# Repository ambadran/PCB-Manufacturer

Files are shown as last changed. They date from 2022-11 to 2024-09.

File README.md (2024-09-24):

# PCB-Manufacturer

###  Intro
A cnc machine with a kinematic mounting mechanism and specialised code to change head as wanted so as to have access to all the
tools to create a PCB without any human intervention.

### Mechanics
This is a 3 Axis CNC machine made of both metal and 3D printed Parts.
The main driving mechanism is a V-wheel on 2020 profile system with a GT-2 belt driving.
Nema17 Motors was used. The machine was designed for maximal repeatability. 

A 3D printed Kinematic Mounting System was developed to enable the CNC machine to detach and attach to different tool heads on command. The current tool heads are a laser head, a spindle, a Pen marker. The machine automatically attaches to the wanted tool heads without any human intervention.

I also developed an auto-clamping system that clamps the PCB in the bed automatically.

#### Photos
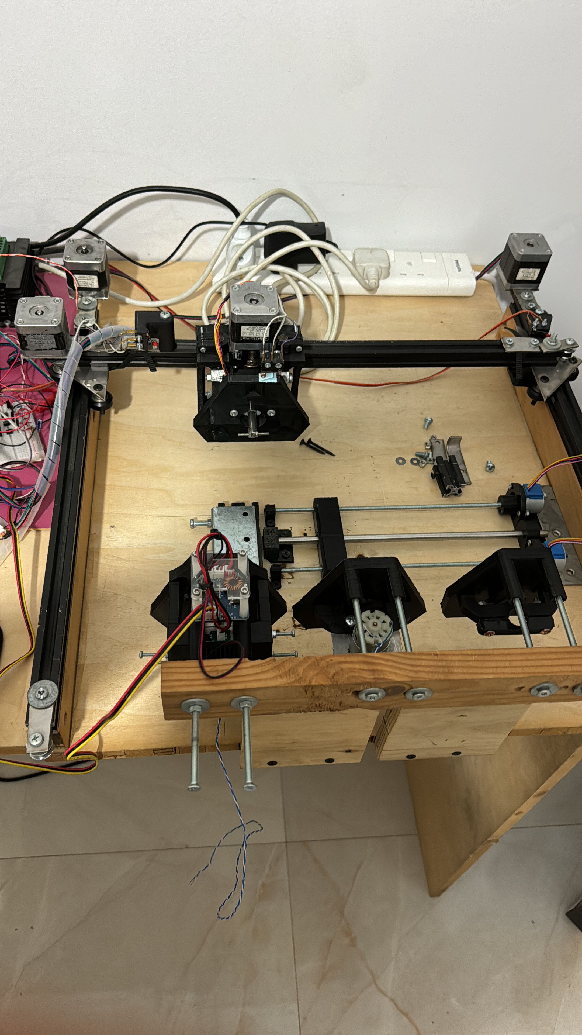
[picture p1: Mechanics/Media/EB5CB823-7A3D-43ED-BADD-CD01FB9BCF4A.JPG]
Overview
[]()

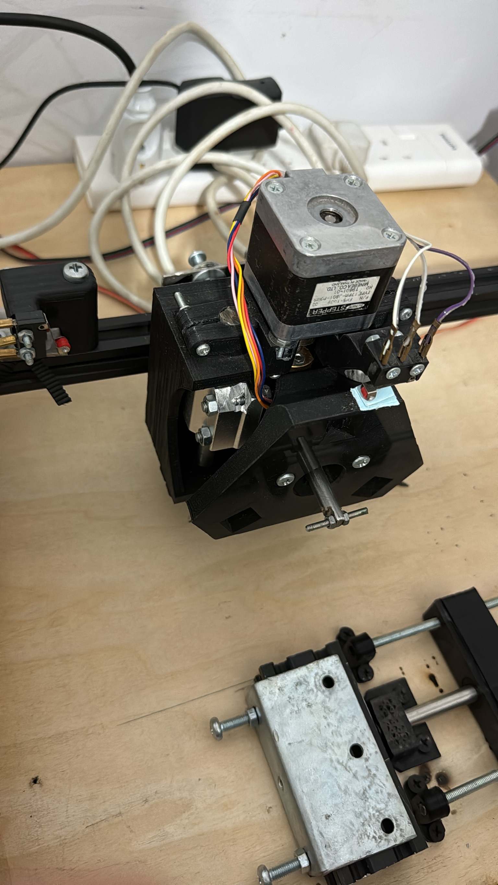
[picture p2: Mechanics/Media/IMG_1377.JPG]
Male Kinematic Mount
[]()

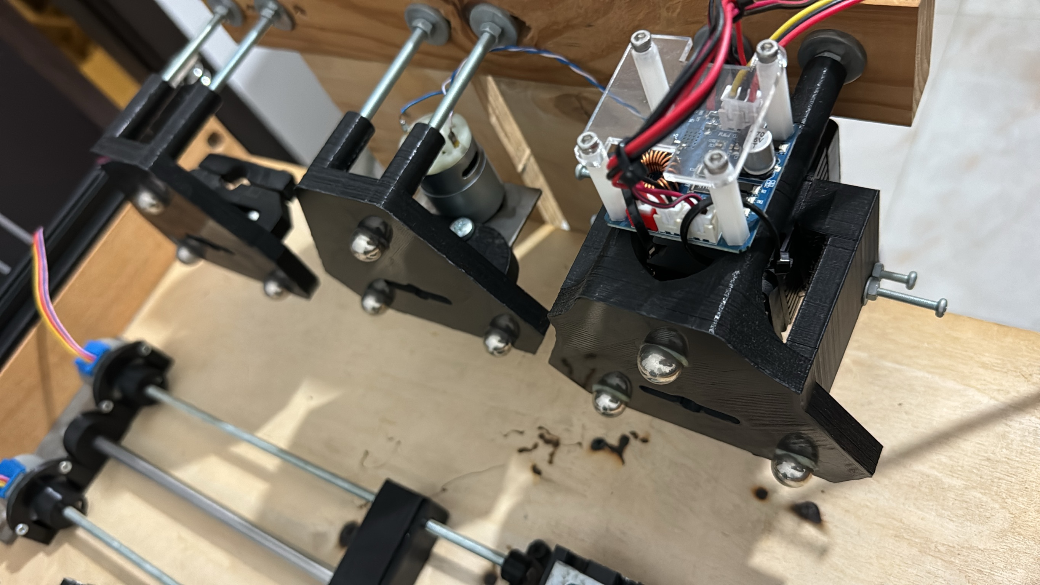
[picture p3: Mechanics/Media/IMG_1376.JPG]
Female Kinematic Mount
[]()

### Electronics
The Main MCU is an Arduino Mega. A Custom GRBL firmware created by me is running on it.

To add a screen monitoring functionality and control the main MCU wirelessly through WiFi, I added a raspberry pi 4 with a 7 inch screen, running mainly UGS Software to monitor the CNC machine.

The Stepper drivers are powerful TB6600 drivers, The end-stops have their own opto-coupler circuit. 
There are 3 power supplies for the CNC machine. one 5v for the main MCU only, one 5v for the raspberry pi. and the third 24v is for the rest of the CNC machine.

This main 24v power supply is switched on using a relay that is controled by the Main MCU. A special G-Code was coded in the firmware to control the main power supply. This adds an important safety layer as the machine is intended to be run remotely.

To relieve the Main MCU from doing everything in the project. I took the liberity to make different circuits for different functions needed for this machine.

I developed a circuit that takes in a 3-bit binary code and the spindle PWM signal from the Main MCU. Then it decodes the 3-bit binary code to allow the PWM to exit through one of the 8 channels that this CNC machine controls. Meaning, the machine can control 8 different end-effectors with PWM, depending on the current 3-bit binary that the MCU outputs.

Another circuit worth mentioning was the stand alone circuit to control the latching mechanism of the kinematic mounting system, where the input to the circuit is just a HIGH/LOW signal from the main MCU triggered by a G-code command `A1` or `A0`. The local MCU does controls the unipolar stepper to latch ON or OFF to the Female kinematic mounts on command and does all the necessary closed-loop logic locally.

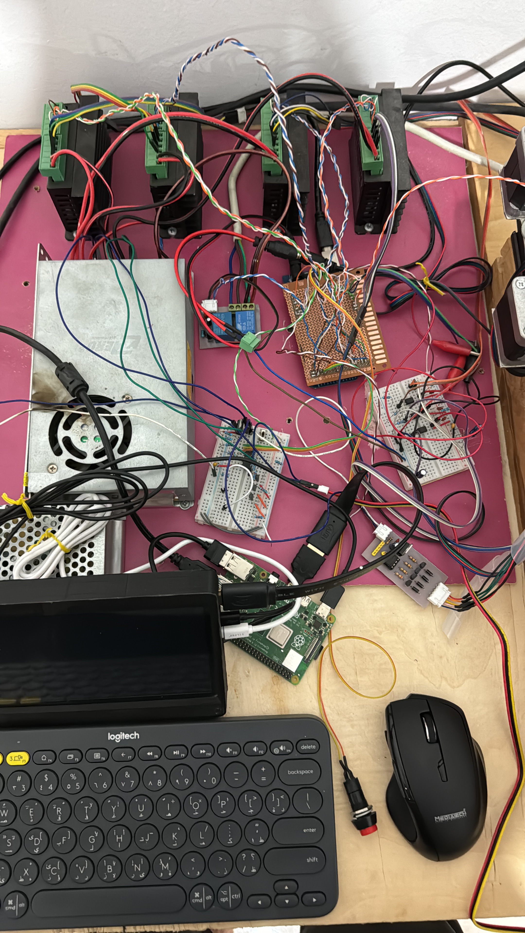
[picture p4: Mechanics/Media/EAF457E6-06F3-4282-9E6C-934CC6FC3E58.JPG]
Electronics
[]()

### Programming
I customized the GRBL firmware from: https://github.com/gnea/grbl 
To accomodate for all the new functionality needed for this CNC machine.
I put in my own G-code commands like `A<x>`, `B<x>` or `C<x>`, that outputs the necessary logic on the Main MCU GPIOs, with no compromise to the original code.

I also developed (from scratch) a complete CAM solution that takes in the gerber files and gives out the G-code ready for my machine. However, due to me deciding to develop from scratch and not use geometry-manipulating libraries like `shapely`. There is alot of corner cases that this version can't handle. 
However, I developed V2 of my all-in-one CAM solution for my CNC machine here: https://github.com/ambadran/PCB-CAM

This version is much much more reliable as to it not being built from scratch.

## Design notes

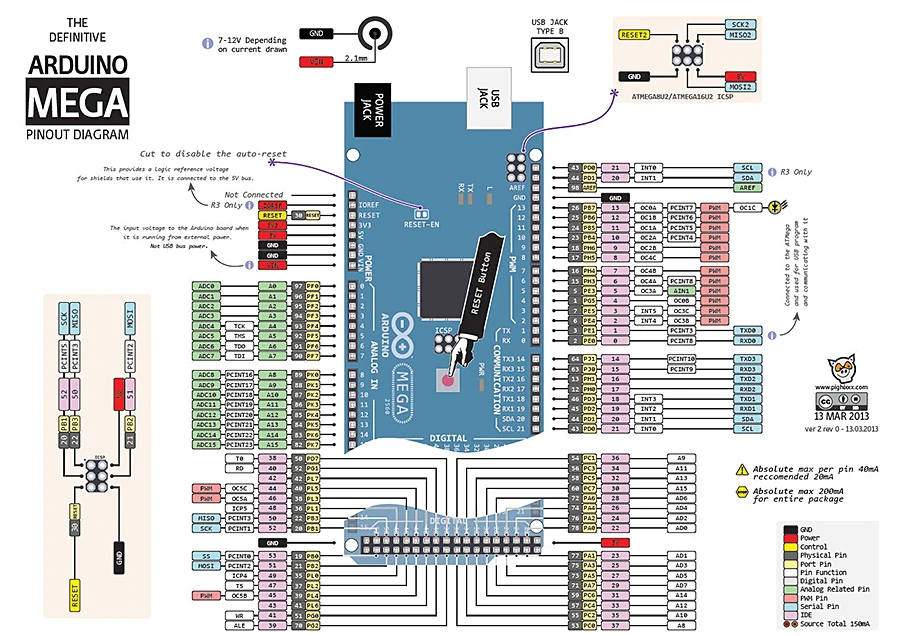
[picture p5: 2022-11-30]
Programming/grbl/photos/arduino-mega-pinout2.png

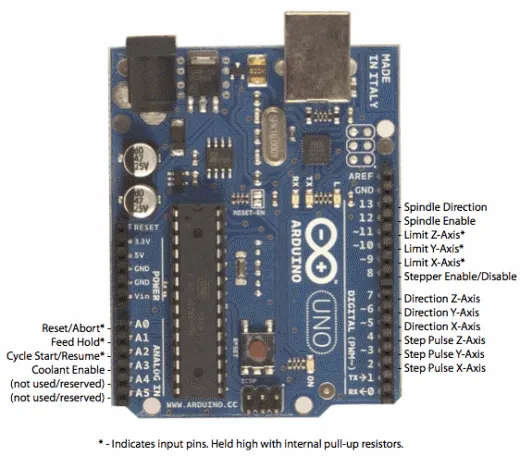
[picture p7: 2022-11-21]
Programming/grbl/photos/grbl_uno_pinout.png

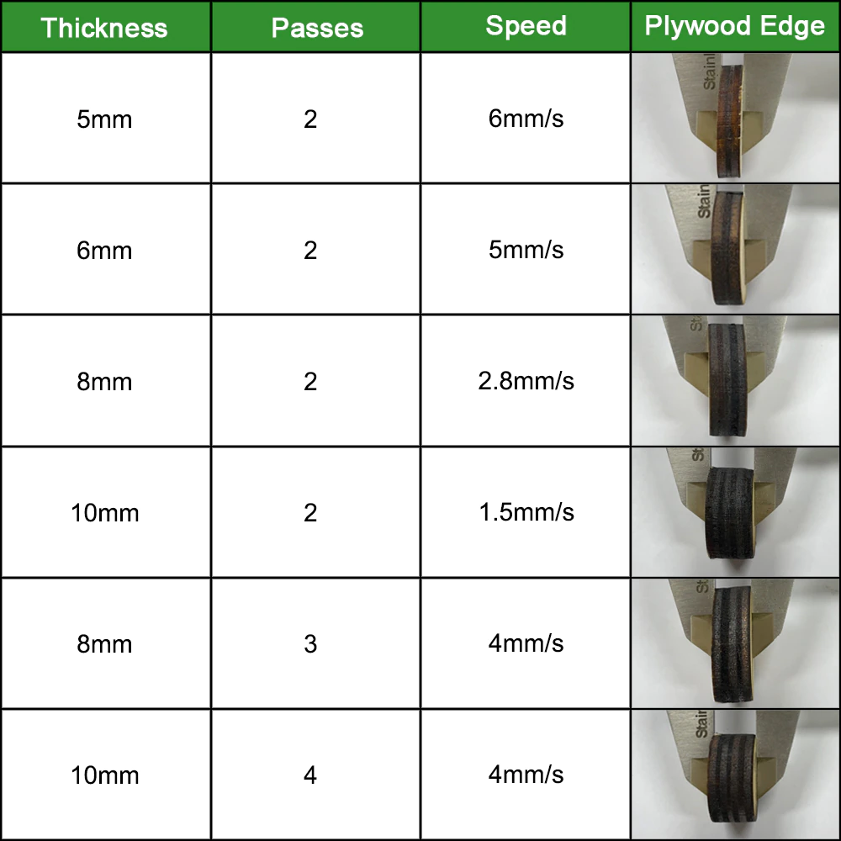
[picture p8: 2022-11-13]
Mechanics/Refrences/Hc2491cd28edc4e7eae7ddbd22f51f325H.jpg.webp

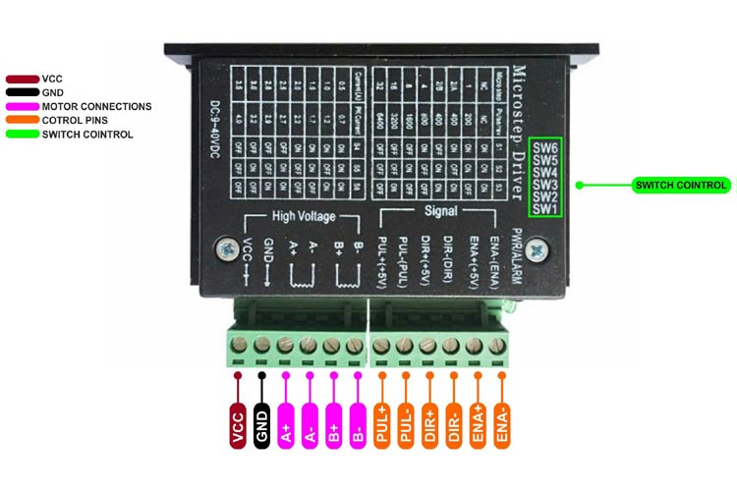
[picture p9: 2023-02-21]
Circuit/bipolar stepper driver/TB6600-Pinout.jpg

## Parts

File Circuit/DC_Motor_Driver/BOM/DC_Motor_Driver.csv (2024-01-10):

Id | Designator | Footprint | Quantity | Designation | Supplier and ref
1 | J1 | JST_EH_S3B-EH_1x03_P2.50mm_Horizontal | 1 | Conn_01x03_Socket
2 | Q3 | TO-92_Inline | 1 | S8550
3 | R3,R2 | R_Axial_DIN0207_L6.3mm_D2.5mm_P7.62mm_Horizontal | 2 | 1k
4 | Q2,Q1,Q4 | TO-92_Inline | 3 | S8050
5 | DC_Motor_Terminal1 | TerminalBlock_bornier-2_P5.08mm | 1 | Screw_Terminal_01x02
6 | Q5 | TO-220-3_Vertical | 1 | IRF540N
7 | R1 | R_Axial_DIN0207_L6.3mm_D2.5mm_P7.62mm_Horizontal | 1 | 10k
8 | CP1 | CP_Radial_D5.0mm_P2.50mm | 1 | 10uF
9 | D1 | D_DO-27_P12.70mm_Horizontal | 1 | SR360
10 | C1 | C_Disc_D5.0mm_W2.5mm_P2.50mm | 1 | 100nF

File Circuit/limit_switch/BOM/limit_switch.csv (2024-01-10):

Id | Designator | Footprint | Quantity | Designation | Supplier and ref
1 | MCU_input1 | JST_EH_S3B-EH_1x03_P2.50mm_Horizontal | 1 | Conn_01x03_Socket
2 | C2,C3,C1 | C_Disc_D5.0mm_W2.5mm_P5.00mm | 3 | 0.1uF
3 | R5,R6,R4 | R_Axial_DIN0207_L6.3mm_D2.5mm_P7.62mm_Horizontal | 3 | 220
4 | Limit_switch_2,Limit_switch_1,Main_PSU_12v1,Limit_switch_3,MCU_5v1 | JST_EH_S2B-EH_1x02_P2.50mm_Horizontal | 5 | Conn_01x02_Socket
5 | OP3,OP2,OP1 | DIP-4_W7.62mm | 3 | PC817
6 | R7,R9,R8 | R_Axial_DIN0207_L6.3mm_D2.5mm_P7.62mm_Horizontal | 3 | 1k
7 | R3,R1,R2 | R_Axial_DIN0207_L6.3mm_D2.5mm_P7.62mm_Horizontal | 3 | 10k

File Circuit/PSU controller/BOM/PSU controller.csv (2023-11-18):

Id | Designator | Footprint | Quantity | Designation | Supplier and ref
1 | D1 | D_DO-34_SOD68_P7.62mm_Horizontal | 1 | D_Schottky
2 | Relay2,Relay1 | Relay_SPDT_SANYOU_SRD_Series_Form_C | 2 | 12v
3 | Q1 | TO-92_Inline | 1 | S8050
4 | CircuitPowerControl1 | PinSocket_1x04_P2.54mm_Vertical | 1 | Conn_01x04_Male
5 | AC_in1,AC_out1 | TerminalBlock_bornier-2_P5.08mm | 2 | Screw_Terminal_01x02
6 | R3 | R_Axial_DIN0207_L6.3mm_D2.5mm_P7.62mm_Horizontal | 1 | 470
7 | R1 | R_Axial_DIN0207_L6.3mm_D2.5mm_P7.62mm_Horizontal | 1 | 10kohm
8 | R2 | R_Axial_DIN0207_L6.3mm_D2.5mm_P7.62mm_Horizontal | 1 | 220
9 | C1 | C_Disc_D5.0mm_W2.5mm_P2.50mm | 1 | 100nF
10 | CP1 | CP_Radial_D5.0mm_P2.00mm | 1 | 100uF
11 | LED1 | D_A-405_P2.54mm_Vertical_AnodeUp | 1 | RED

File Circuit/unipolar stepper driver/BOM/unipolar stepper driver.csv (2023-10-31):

Id | Designator | Footprint | Quantity | Designation | Supplier and ref
1 | Q2,Q4,Q1,Q3 | TO-92_Inline | 4 | S8050
2 | R4,R3 | R_Axial_DIN0207_L6.3mm_D2.5mm_P7.62mm_Horizontal | 2 | 330
3 | C1 | C_Disc_D3.0mm_W2.0mm_P2.50mm | 1 | 10nF
4 | DebuggerPins1,Output1 | PinHeader_1x05_P2.54mm_Vertical | 2 | Conn_01x05_Female
5 | Input1 | PinHeader_1x03_P2.54mm_Vertical | 1 | Conn_01x03_Female
6 | R1,R2 | R_Axial_DIN0207_L6.3mm_D2.5mm_P7.62mm_Horizontal | 2 | 300
7 | D3,D4,D1,D2 | D_DO-34_SOD68_P7.62mm_Horizontal | 4 | DIODE
8 | Debug/UART_pin1 | PinSocket_1x01_P2.54mm_Vertical | 1 | Conn_01x01_Socket
9 | uC1 | DIP-8_W7.62mm | 1 | PIC12F675-IP
10 | PowerRegulator1 | TO-220-3_Vertical | 1 | LM7805_TO220
11 | CP1 | CP_Radial_D5.0mm_P2.50mm | 1 | C_Polarized
12 | R5 | R_Axial_DIN0207_L6.3mm_D2.5mm_P7.62mm_Horizontal | 1 | 10k

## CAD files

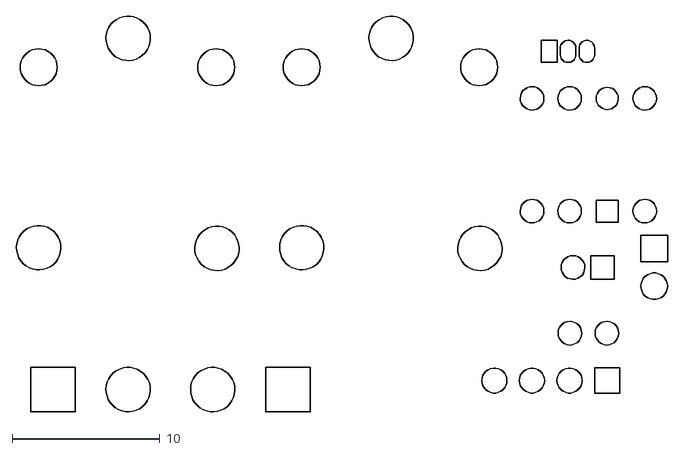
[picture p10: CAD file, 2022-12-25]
Circuit/PSU controller/DXF/PSU controller-B_Cu.dxf
44.0 x 26.7

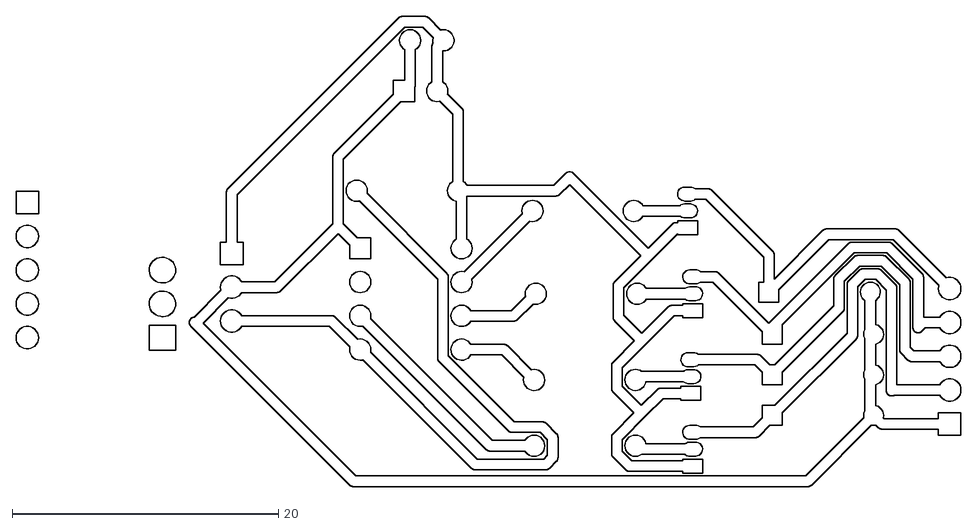
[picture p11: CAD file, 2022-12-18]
Circuit/unipolar stepper driver/DXF/unipolar stepper driver-F_Cu.dxf
71.0 x 35.3

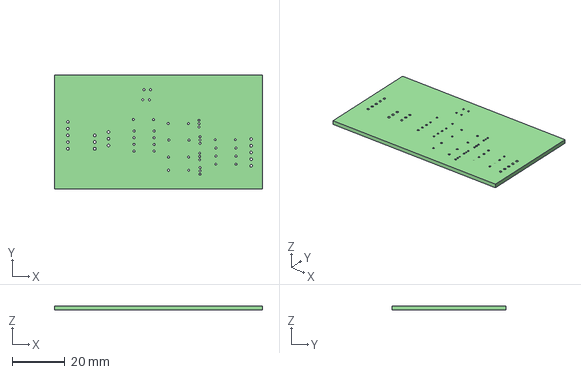
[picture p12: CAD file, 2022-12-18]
Circuit/unipolar stepper driver/STEP/unipolar stepper driver.step
78.7 x 43.2 x 1.60 mm

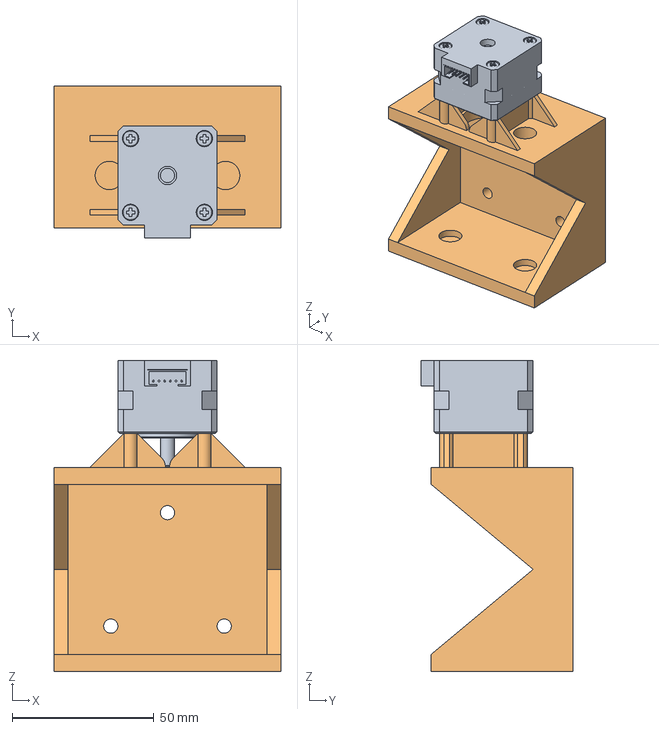
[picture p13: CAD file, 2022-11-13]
Mechanics/3mf/y&z.3mf
80.0 x 53.5 x 109.7 mm
MINEBEA_05701202

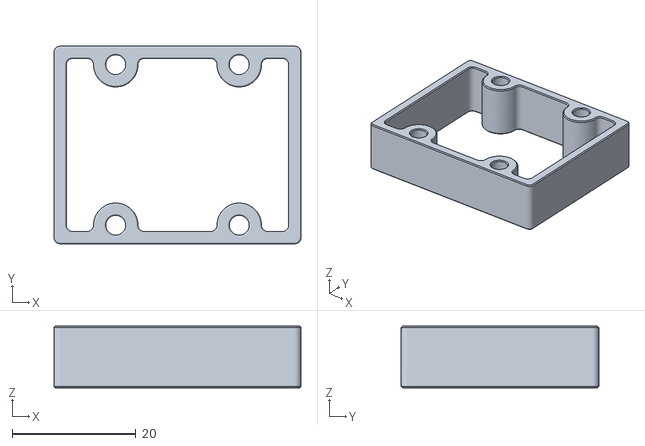
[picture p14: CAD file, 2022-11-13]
Mechanics/reference CAD/Tool Changer/ToolChanger-master/Hemera Direct Tool/STLs/V6_Receiver_Top.stl
40.0 x 32.0 x 10.0

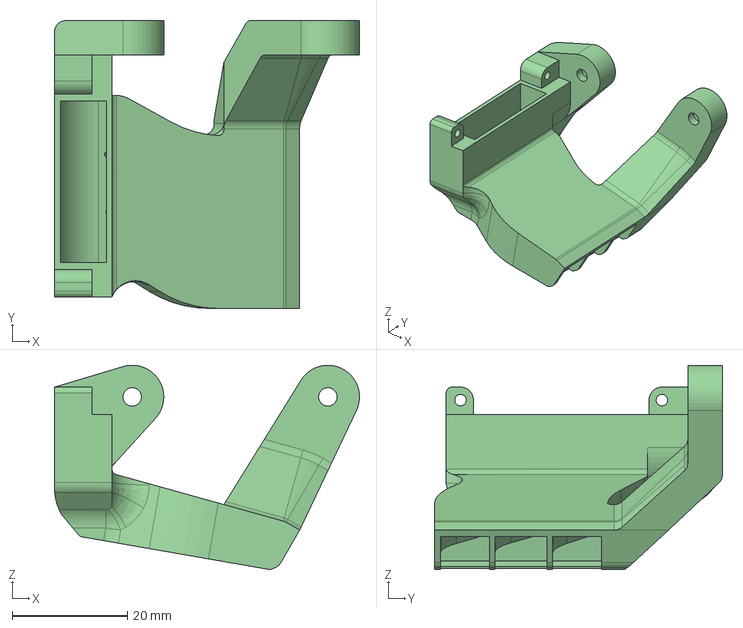
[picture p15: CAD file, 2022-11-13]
Mechanics/reference CAD/Tool Changer/ToolChanger-master/Hemera Direct Tool/STPs/Hemera_PCF_Duct_-_Volcano.step
53.0 x 50.0 x 35.5 mm

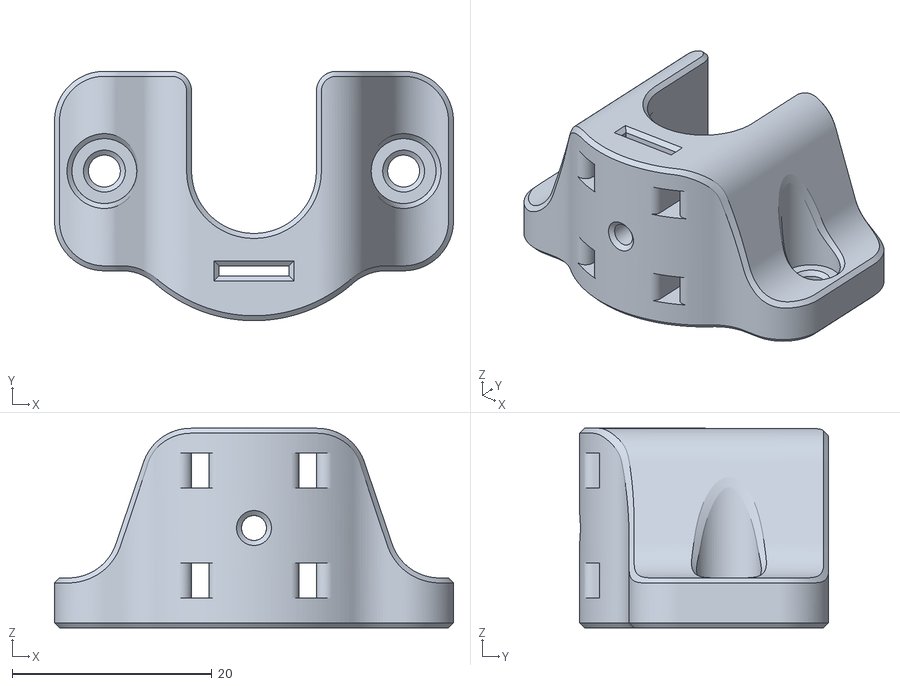
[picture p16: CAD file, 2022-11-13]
Mechanics/reference CAD/Tool Changer/ToolChanger-master/STLs/X-Carriage Cables.stl
40.0 x 25.0 x 20.0

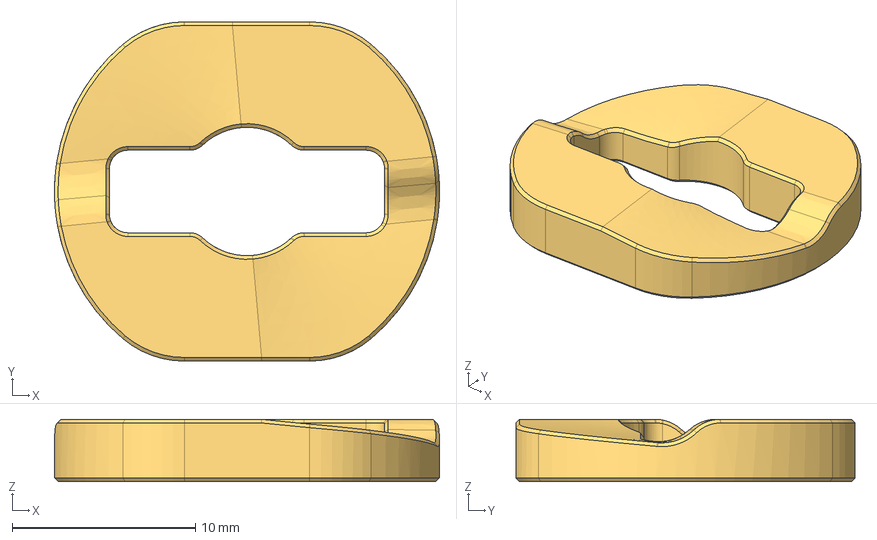
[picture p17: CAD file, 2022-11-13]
Mechanics/reference CAD/Tool Changer/ToolChanger-master/STPs/TC-RAMP-6MM 1.3.step
21.0 x 18.5 x 3.40 mm

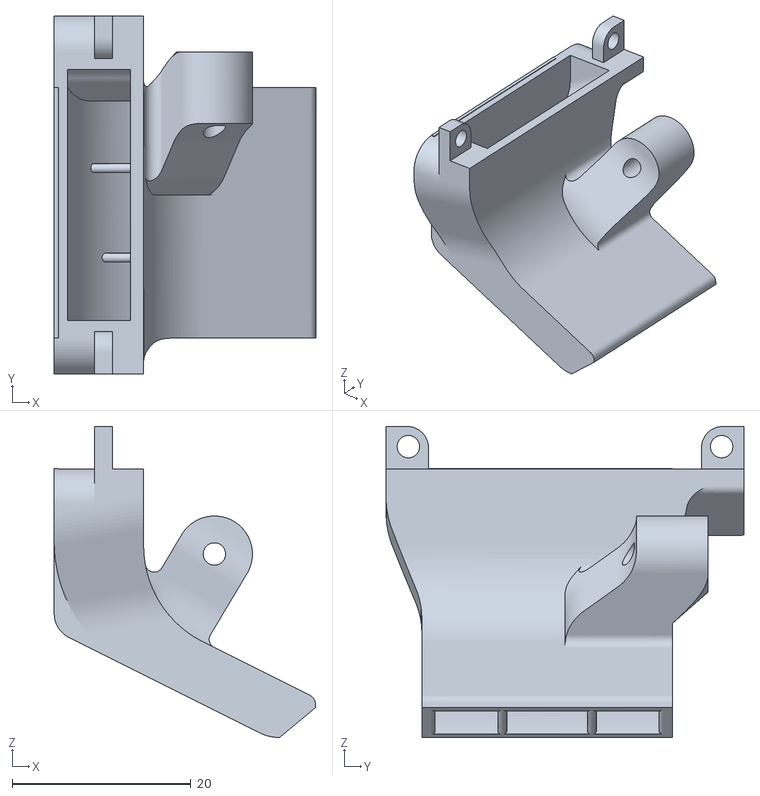
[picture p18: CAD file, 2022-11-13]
Mechanics/reference CAD/Tool Changer/ToolChanger-master/V6 Tool/STLs/V6 PCF Duct (Winsinn).stl
29.2 x 40.0 x 34.8

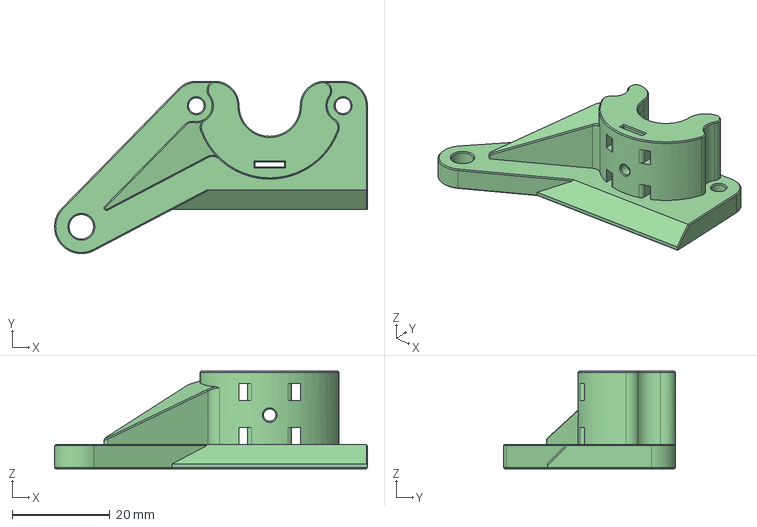
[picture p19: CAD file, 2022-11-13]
Mechanics/reference CAD/Tool Changer/ToolChanger-master/V6 Tool/STPs/V6 Dock Cables.step
64.0 x 35.2 x 20.0 mm

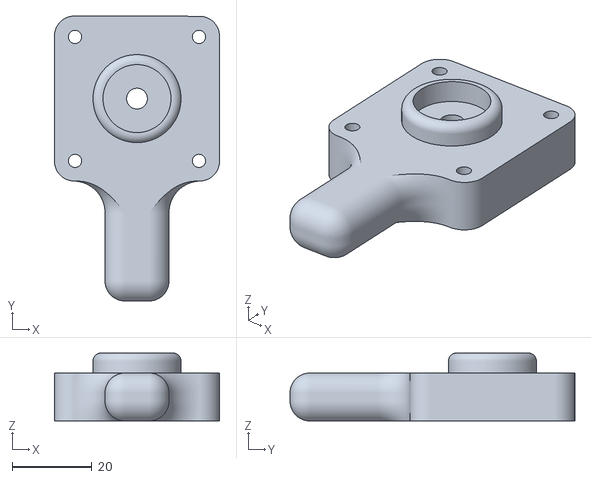
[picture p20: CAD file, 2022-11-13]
Mechanics/STLs/Nema 17 holes Spacer.stl
41.3 x 71.3 x 17.0

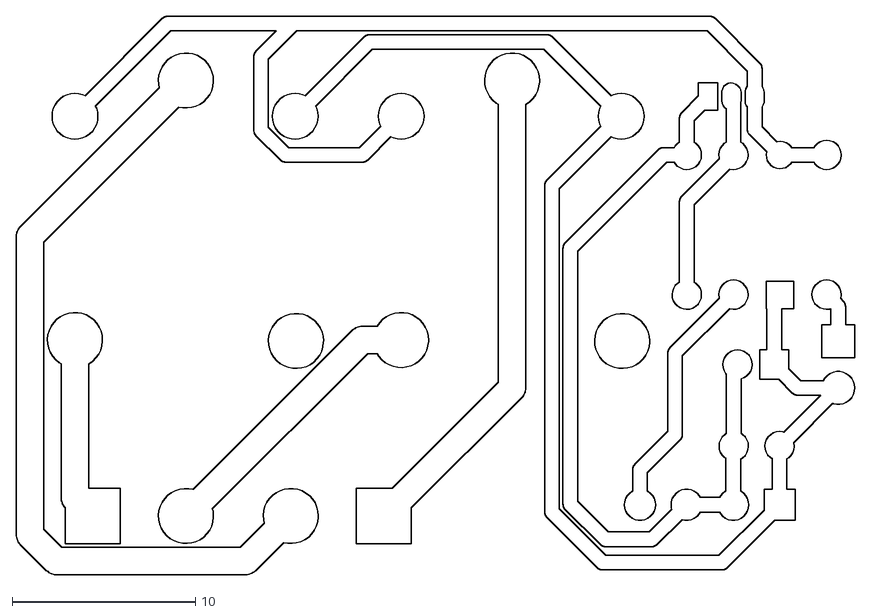
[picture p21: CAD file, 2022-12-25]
Circuit/PSU controller/DXF/PSU controller-F_Cu.dxf
45.7 x 30.4

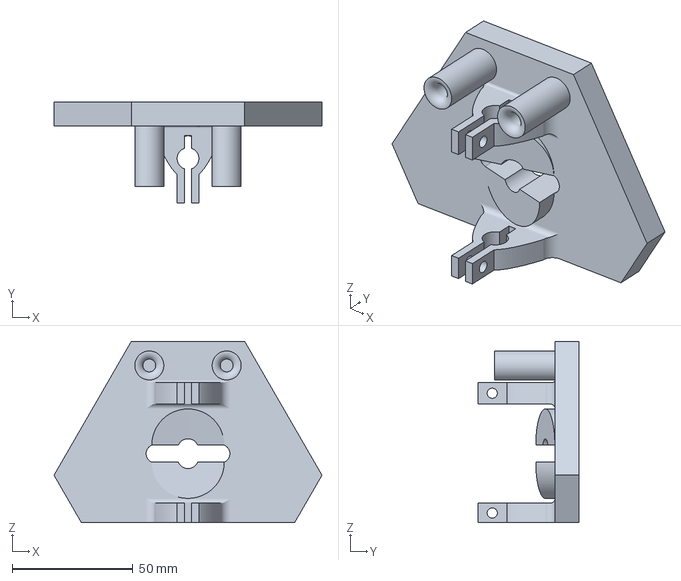
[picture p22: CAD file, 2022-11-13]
Mechanics/3mf/female.3mf
110.9 x 42.0 x 75.1 mm

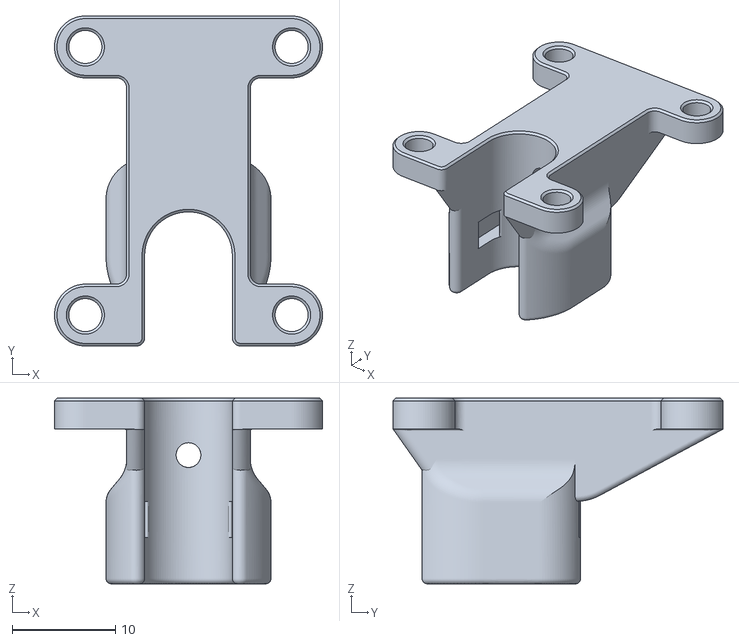
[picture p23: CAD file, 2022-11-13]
Mechanics/reference CAD/Tool Changer/ToolChanger-master/Hemera Direct Tool/STLs/V6_Cable_Support.stl
26.0 x 32.0 x 18.0

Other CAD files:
Mechanics/reference CAD/Tool Changer/ToolChanger-master/Hemera Direct Tool/STPs/TC-V6-HEMERA-DOCK-BRACE.step
Mechanics/reference CAD/Tool Changer/ToolChanger-master/STLs/Tool-Changer Cover Triangle.stl
Mechanics/reference CAD/Tool Changer/ToolChanger-master/STPs/TC-MOD0.5-40T-GEAR 1.1.step
Mechanics/reference CAD/Tool Changer/ToolChanger-master/V6 Tool/STLs/V6 Dock Cables(Mirror).stl
Circuit/PSU controller/DXF/PSU controller-B_Paste.dxf
Circuit/PSU controller/DXF/PSU controller-B_Silkscreen.dxf
Circuit/PSU controller/DXF/PSU controller-Edge_Cuts.dxf
Circuit/PSU controller/DXF/PSU controller-F_Paste.dxf
Circuit/PSU controller/DXF/PSU controller-F_Silkscreen.dxf
Mechanics/3mf/Male.3mf
Mechanics/3mf/Y and Z.3mf
Mechanics/3mf/Y-Bracket.3mf
Mechanics/STLs/laser_module_k_mount.stl
Mechanics/reference CAD/Tool Changer/ToolChanger-master/Hemera Direct Tool/STLs/Hemera_PCF_Bracket.stl
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

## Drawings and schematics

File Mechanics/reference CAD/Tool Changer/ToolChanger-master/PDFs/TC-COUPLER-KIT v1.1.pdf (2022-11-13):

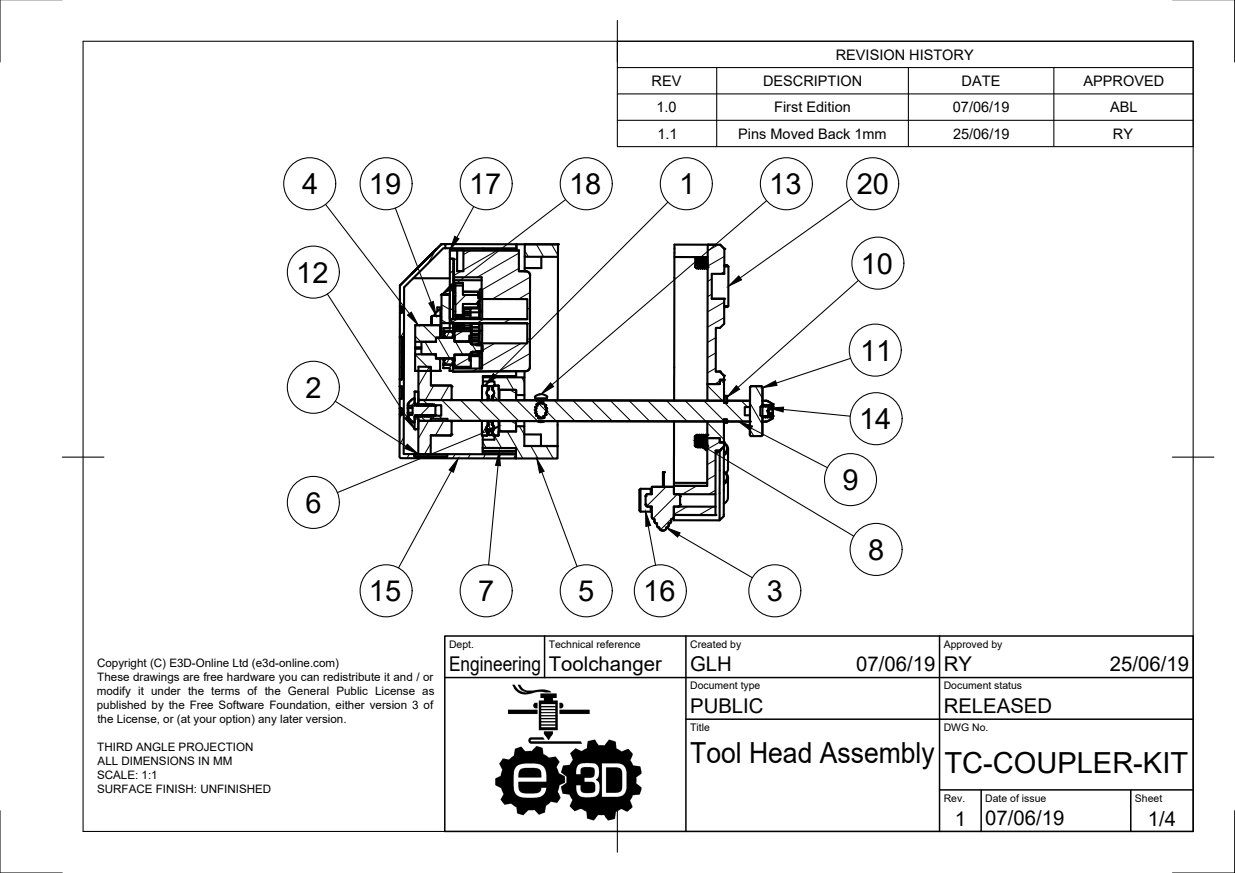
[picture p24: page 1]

REVISION HISTORY

REV | DESCRIPTION | DATE | APPROVED
1.0 | First Edition | 07/06/19 | ABL
1.1 | Pins Moved Back 1mm | 25/06/19 | RY

Dept. Engineering | Technical reference Toolchanger | Created by GLH 07/06/19 | Approved by RY 25/06/19

Copyright (C) E3D-Online Ltd (e3d-online.com)
These drawings are free hardware you can redistribute it and / or modify it under the terms of the General Public License as published by the Free Software Foundation, either version 3 of

Document type PUBLIC | Document status RELEASED

the License, or (at your option) any later version.

Title | DWG No. TC-COUPLER-KIT Tool Head Assembly

THIRD ANGLE PROJECTION
ALL DIMENSIONS IN MM
SCALE: 1:1
SURFACE FINISH: UNFINISHED

Rev. 1 | Date of issue 07/06/19 | Sheet

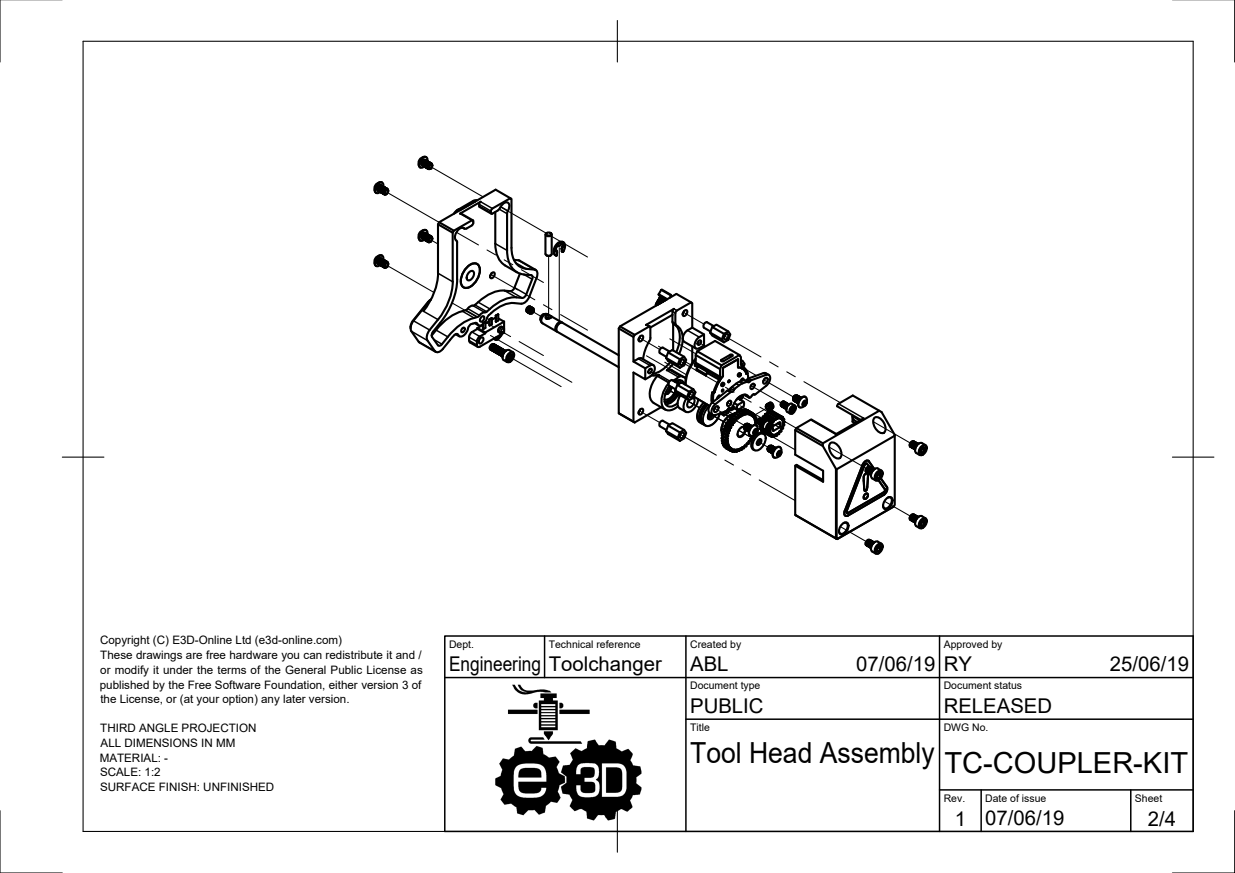
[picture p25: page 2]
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

Dept. Engineering | Technical reference Toolchanger | Created by ABL 07/06/19 | Approved by RY 25/06/19

Document type PUBLIC | Document status RELEASED

the License, or (at your option) any later version.

THIRD ANGLE PROJECTION
ALL DIMENSIONS IN MM
MATERIAL: -
SCALE: 1:2
SURFACE FINISH: UNFINISHED

Title | DWG No. TC-COUPLER-KIT Tool Head Assembly

Rev. | Date of issue | Sheet

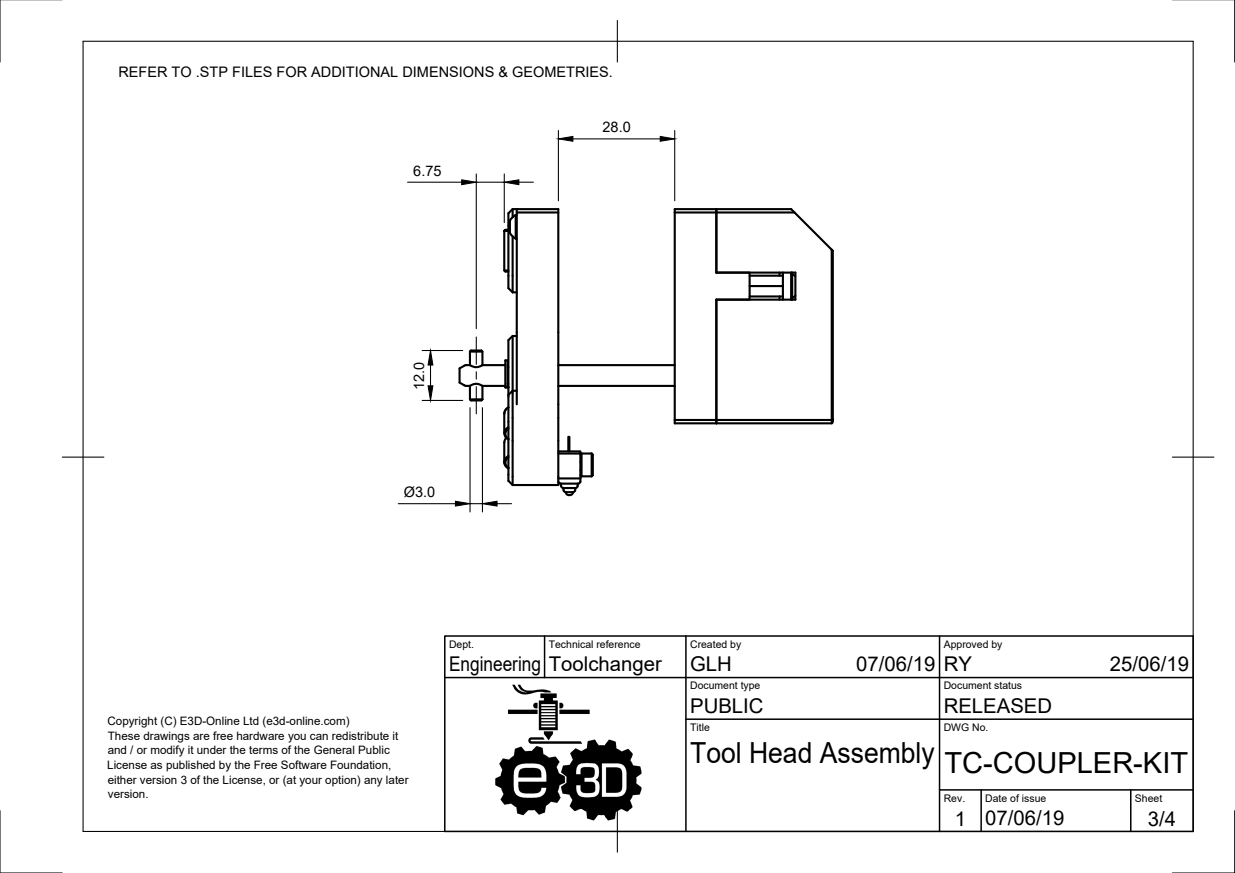
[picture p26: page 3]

REFER TO .STP FILES FOR ADDITIONAL DIMENSIONS & GEOMETRIES.

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

Document type PUBLIC | Document status RELEASED

Copyright (C) E3D-Online Ltd (e3d-online.com)
These drawings are free hardware you can redistribute it
and / or modify it under the terms of the General Public
License as published by the Free Software Foundation,
either version 3 of the License, or (at your option) any later
version.

Title | DWG No. TC-COUPLER-KIT Tool Head Assembly

Rev. | Date of issue | Sheet

Dept. Engineering | Technical reference Toolchanger | Created by GLH 07/06/19 | Approved by RY 25/06/19
| | Document type PUBLIC | Document status RELEASED
| | Title | DWG No. TC-COUPLER-KIT Tool Head Assembly
Rev. | Date of issue | Sheet

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

### Parts List

Item | Qty | Description
1 | 1 | F5-12M Thrust Bearing
2 | 1 | 40T Gear M0D 0.5
3 | 1 | Endstop Switch
4 | 1 | 20T Gear MOD 0.5
5 | 1 | TC-BACK
6 | 1 | MR105RS Bearing
7 | 1 | 8mm Standoff
8 | 7 | M4 5mm Button Head Screw
9 | 1 | Tool Coupler Shaft
10 | 1 | E-Clip
11 | 1 | 12mm x 3mm Dowel Pin
12 | 1 | M3 Washer
13 | 5 | M3 4mm Socket Head Screw
14 | 2 | M3 3mm Grub Screw
15 | 1 | Printed Cover
16 | 1 | M3 10mm Socket Head Screw
17 | 1 | Stepper Motor
18 | 1 | Motor Bracket
19 | 2 | M2.5 5mm Socket Head Screw
20 | 1 | TC-FACE-AS

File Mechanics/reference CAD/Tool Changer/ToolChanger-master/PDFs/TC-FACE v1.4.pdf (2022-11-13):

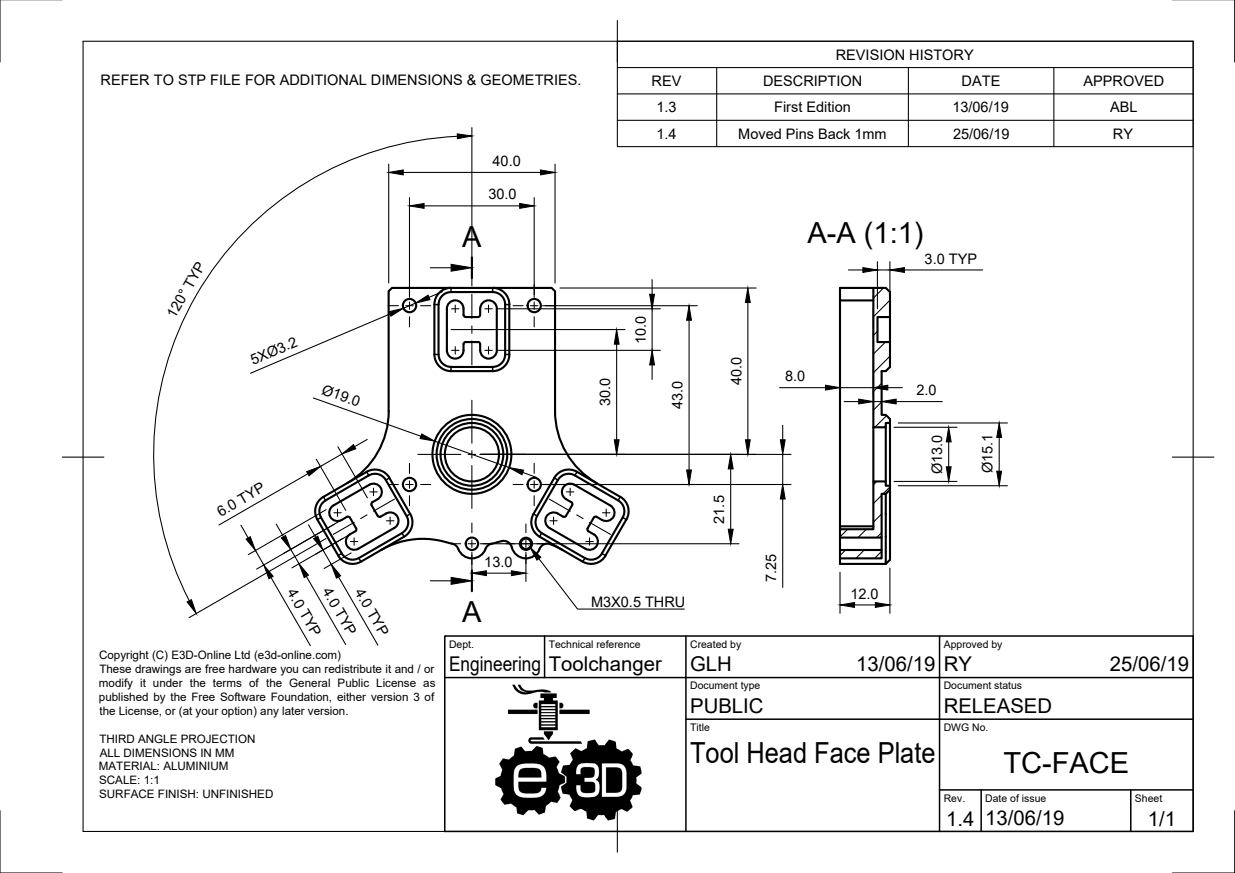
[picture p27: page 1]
M3X0.5 THRU; 120° TYP 43.0 Ø13.0 Ø15.1; 3.0 TYP; 6.0 TYP

REVISION HISTORY

REFER TO STP FILE FOR ADDITIONAL DIMENSIONS & GEOMETRIES.

REV | DESCRIPTION | DATE | APPROVED
1.3 | First Edition | 13/06/19 | ABL
1.4 | Moved Pins Back 1mm | 25/06/19 | RY

4.0 TYP 4.0 TYP 4.0 TYP

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

Dept. Engineering | Technical reference Toolchanger | Created by GLH 13/06/19 | Approved by RY 25/06/19

Document type PUBLIC | Document status RELEASED

the License, or (at your option) any later version.

Title | DWG No. TC-FACE Tool Head Face Plate

THIRD ANGLE PROJECTION
ALL DIMENSIONS IN MM
MATERIAL: ALUMINIUM
SCALE: 1:1
SURFACE FINISH: UNFINISHED

Rev. 1.4 | Date of issue 13/06/19 | Sheet 1/1

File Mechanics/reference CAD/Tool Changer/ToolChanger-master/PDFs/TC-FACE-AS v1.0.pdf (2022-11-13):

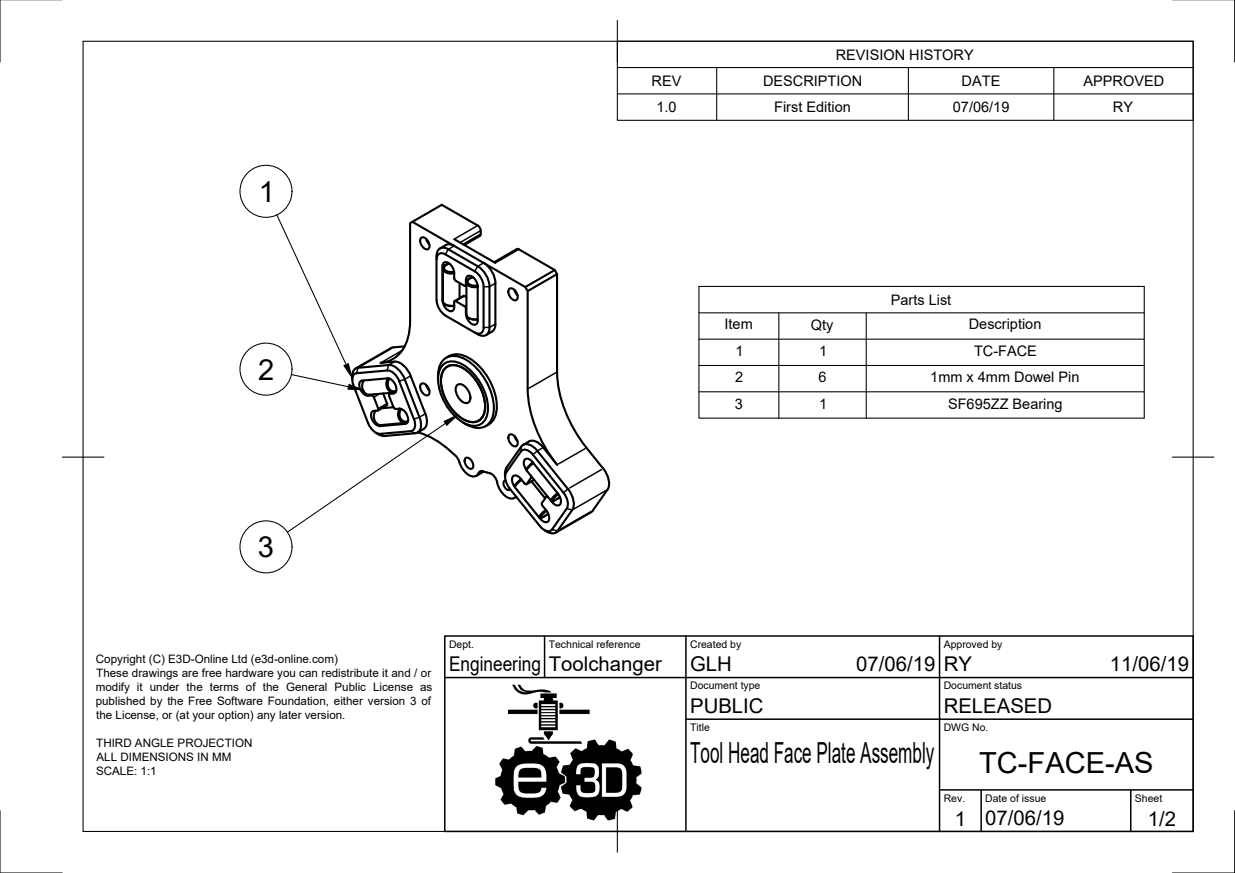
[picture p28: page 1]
Parts List

REVISION HISTORY

REV | DESCRIPTION | DATE | APPROVED
1.0 | First Edition | 07/06/19 | RY

Item | Qty | Description
1 | 1 | TC-FACE
2 | 6 | 1mm x 4mm Dowel Pin
3 | 1 | SF695ZZ Bearing

Dept. Engineering | Technical reference Toolchanger | Created by GLH 07/06/19 | Approved by RY 11/06/19

Copyright (C) E3D-Online Ltd (e3d-online.com)
These drawings are free hardware you can redistribute it and / or modify it under the terms of the General Public License as published by the Free Software Foundation, either version 3 of

Document type PUBLIC | Document status RELEASED

the License, or (at your option) any later version.

Title | DWG No. TC-FACE-AS Tool Head Face Plate Assembly

THIRD ANGLE PROJECTION
ALL DIMENSIONS IN MM
SCALE: 1:1

Rev. 1 | Date of issue 07/06/19 | Sheet 1/2

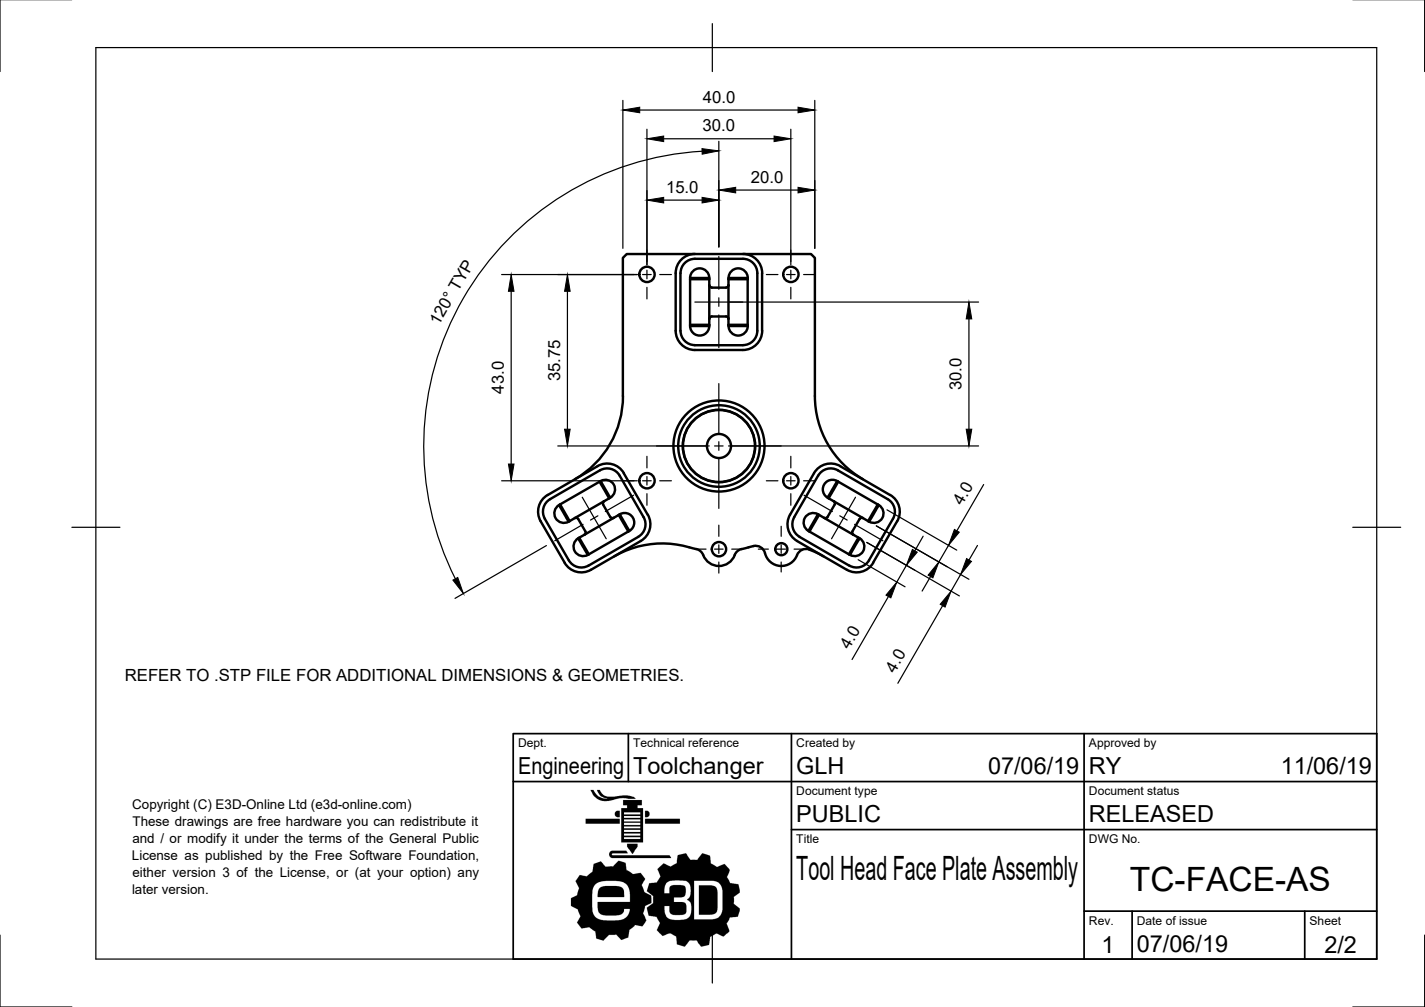
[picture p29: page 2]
120° TYP

REFER TO .STP FILE FOR ADDITIONAL DIMENSIONS & GEOMETRIES.

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

Document type PUBLIC | Document status RELEASED

Copyright (C) E3D-Online Ltd (e3d-online.com)
These drawings are free hardware you can redistribute it
and / or modify it under the terms of the General Public
License as published by the Free Software Foundation,
either version 3 of the License, or (at your option) any
later version.

Title | DWG No. TC-FACE-AS Tool Head Face Plate Assembly

Rev. 1 | Date of issue 07/06/19 | Sheet 2/2

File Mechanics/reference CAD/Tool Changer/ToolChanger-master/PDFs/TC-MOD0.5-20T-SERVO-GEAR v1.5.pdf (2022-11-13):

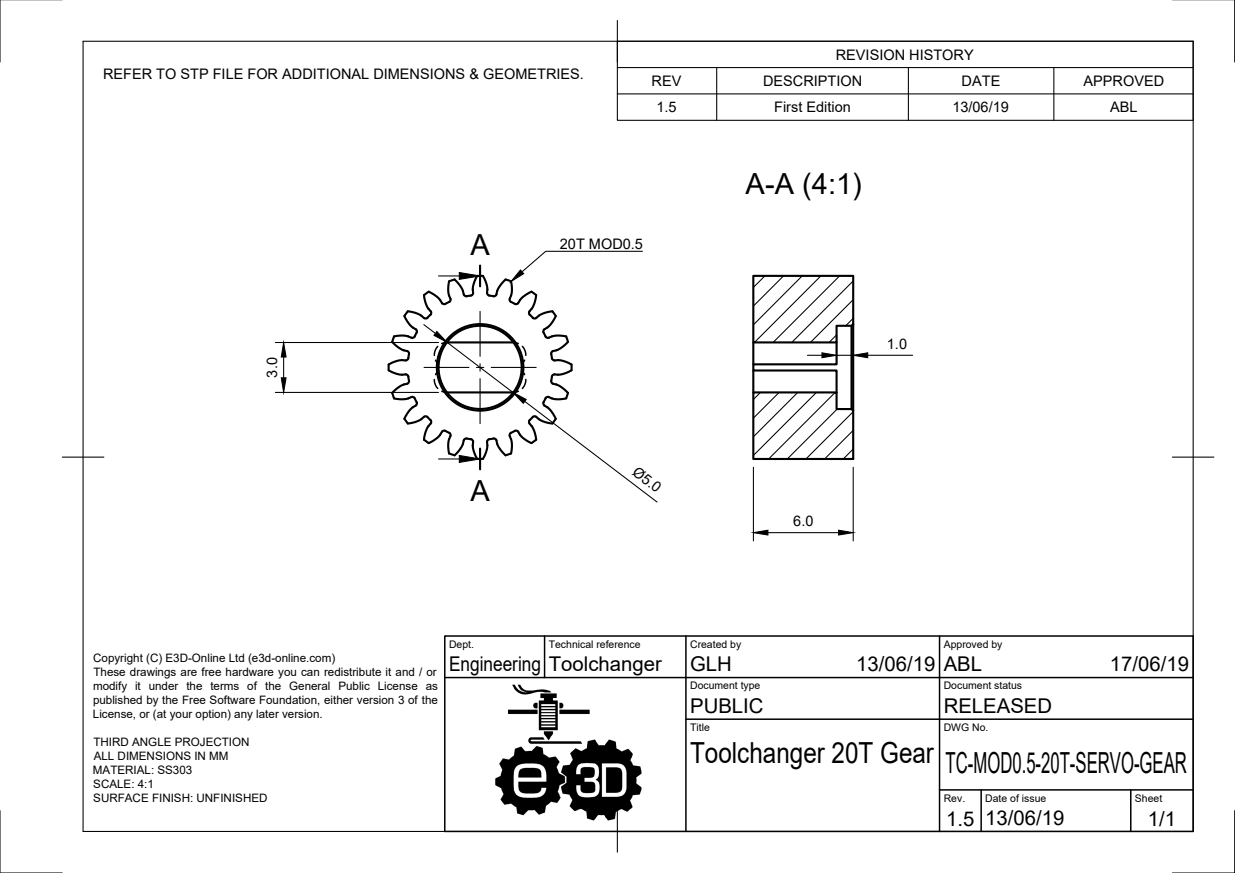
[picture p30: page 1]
20T MOD0.5

REVISION HISTORY

REFER TO STP FILE FOR ADDITIONAL DIMENSIONS & GEOMETRIES.

REV | DESCRIPTION | DATE | APPROVED
1.5 | First Edition | 13/06/19 | ABL

Dept. Engineering | Technical reference Toolchanger | Created by GLH 13/06/19 | Approved by ABL 17/06/19

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

Document type PUBLIC | Document status RELEASED

License, or (at your option) any later version.

Title | DWG No. TC-MOD0.5-20T-SERVO-GEAR Toolchanger 20T Gear

THIRD ANGLE PROJECTION
ALL DIMENSIONS IN MM
MATERIAL: SS303
SCALE: 4:1
SURFACE FINISH: UNFINISHED

Rev. 1.5 | Date of issue 13/06/19 | Sheet 1/1

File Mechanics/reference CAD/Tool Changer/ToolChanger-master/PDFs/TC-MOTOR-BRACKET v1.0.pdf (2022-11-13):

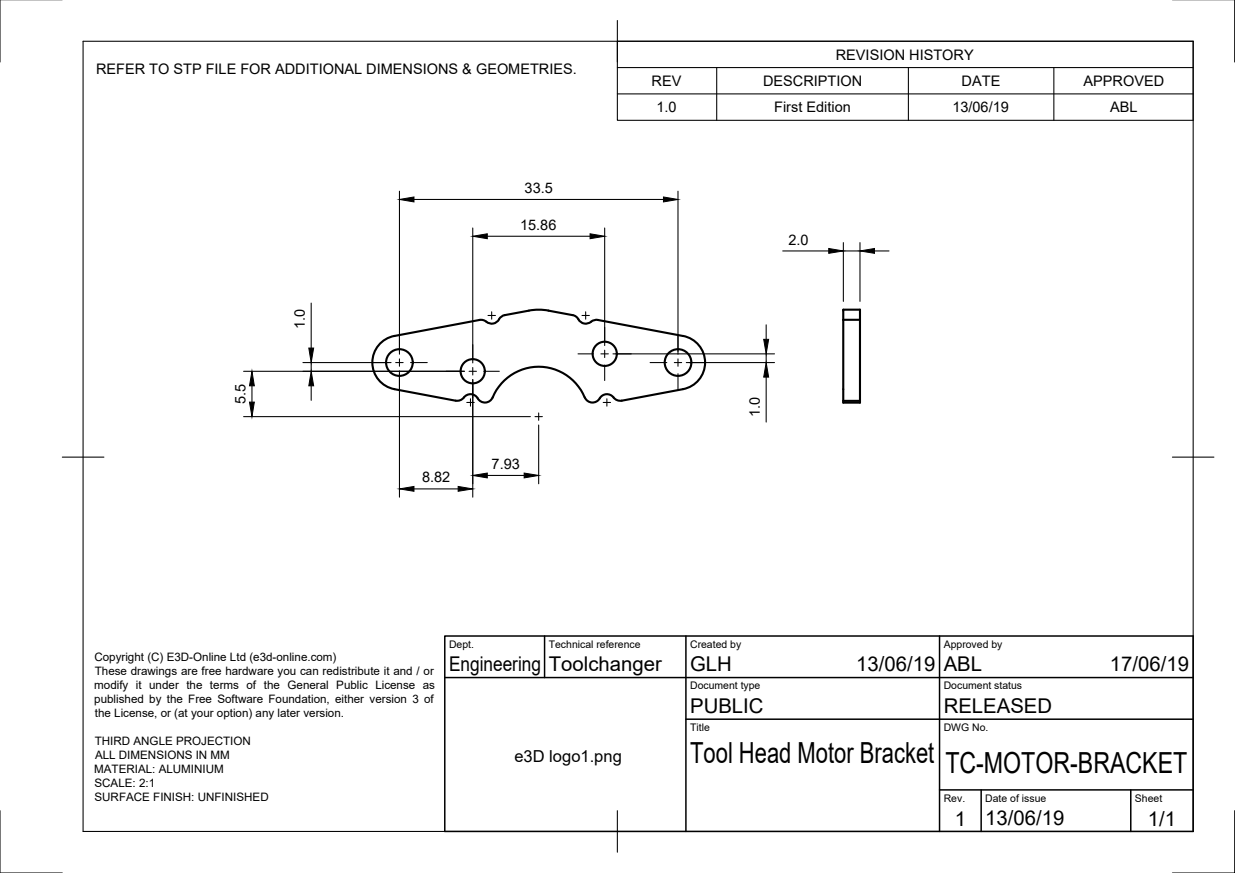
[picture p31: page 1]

REVISION HISTORY

REFER TO STP FILE FOR ADDITIONAL DIMENSIONS & GEOMETRIES.

REV | DESCRIPTION | DATE | APPROVED
1.0 | First Edition | 13/06/19 | ABL

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

e3D logo1.png | | Document type PUBLIC | Document status RELEASED

the License, or (at your option) any later version.

Title | DWG No. TC-MOTOR-BRACKET Tool Head Motor Bracket

THIRD ANGLE PROJECTION
ALL DIMENSIONS IN MM
MATERIAL: ALUMINIUM
SCALE: 2:1
SURFACE FINISH: UNFINISHED

Rev. 1 | Date of issue 13/06/19 | Sheet 1/1

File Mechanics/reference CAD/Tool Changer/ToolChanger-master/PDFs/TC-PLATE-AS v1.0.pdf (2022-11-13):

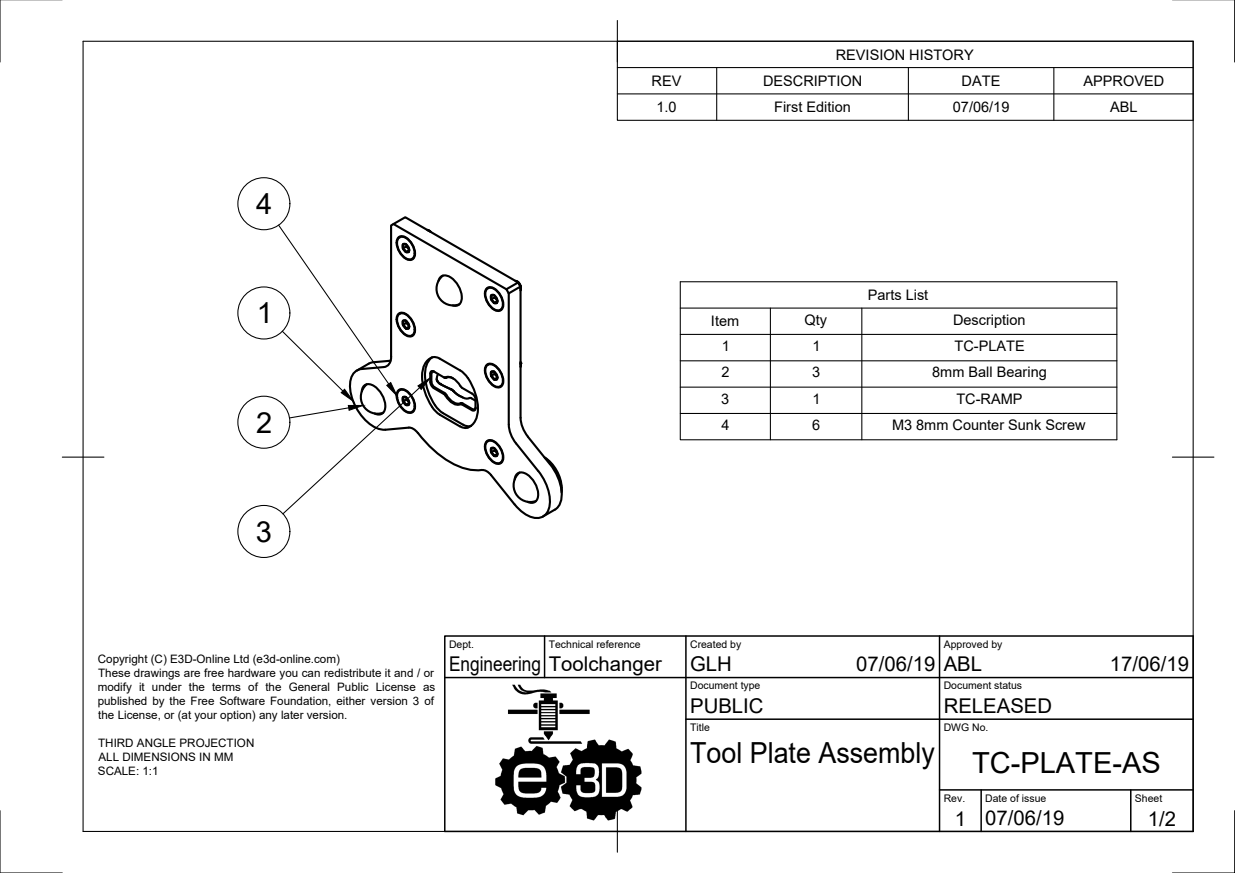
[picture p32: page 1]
Parts List

REVISION HISTORY

REV | DESCRIPTION | DATE | APPROVED
1.0 | First Edition | 07/06/19 | ABL

Item | Qty | Description
1 | 1 | TC-PLATE
2 | 3 | 8mm Ball Bearing
3 | 1 | TC-RAMP
4 | 6 | M3 8mm Counter Sunk Screw

Dept. Engineering | Technical reference Toolchanger | Created by GLH 07/06/19 | Approved by ABL 17/06/19

Copyright (C) E3D-Online Ltd (e3d-online.com)
These drawings are free hardware you can redistribute it and / or modify it under the terms of the General Public License as published by the Free Software Foundation, either version 3 of

Document type PUBLIC | Document status RELEASED

the License, or (at your option) any later version.

Title | DWG No. TC-PLATE-AS Tool Plate Assembly

THIRD ANGLE PROJECTION
ALL DIMENSIONS IN MM
SCALE: 1:1

Rev. 1 | Date of issue 07/06/19 | Sheet 1/2

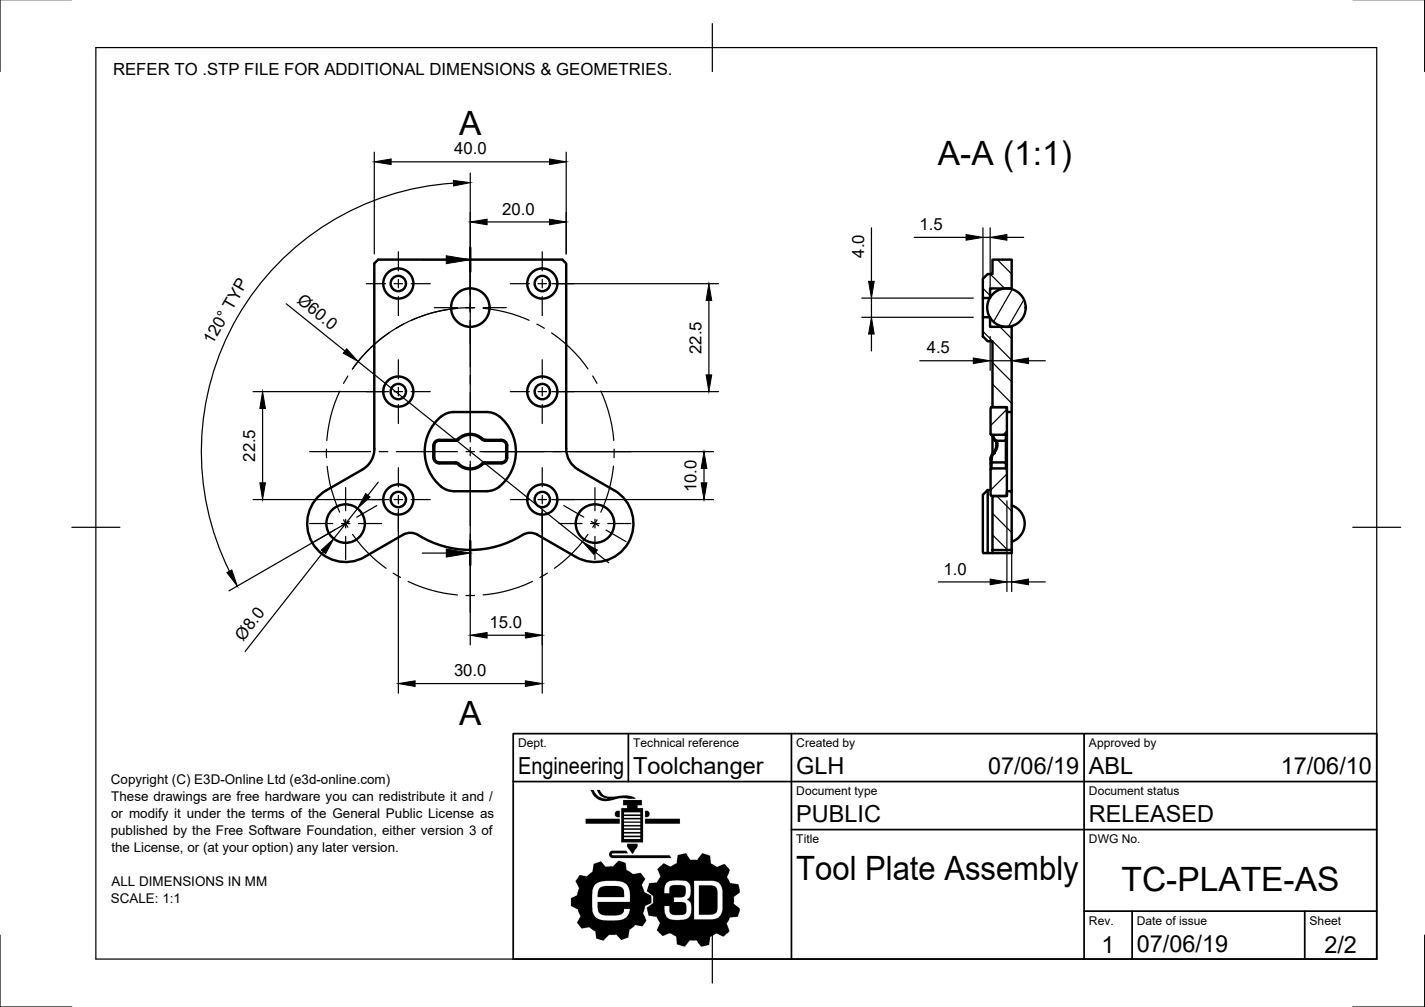
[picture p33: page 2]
Ø60.0 120° TYP

REFER TO .STP FILE FOR ADDITIONAL DIMENSIONS & GEOMETRIES.

Dept. Engineering | Technical reference Toolchanger | Created by GLH 07/06/19 | Approved by ABL Copyright (C) E3D-Online Ltd (e3d-online.com) 17/06/10

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

Document type PUBLIC | Document status RELEASED

the License, or (at your option) any later version.

Title | DWG No. TC-PLATE-AS Tool Plate Assembly

ALL DIMENSIONS IN MM
SCALE: 1:1

Rev. 1 | Date of issue 07/06/19 | Sheet 2/2

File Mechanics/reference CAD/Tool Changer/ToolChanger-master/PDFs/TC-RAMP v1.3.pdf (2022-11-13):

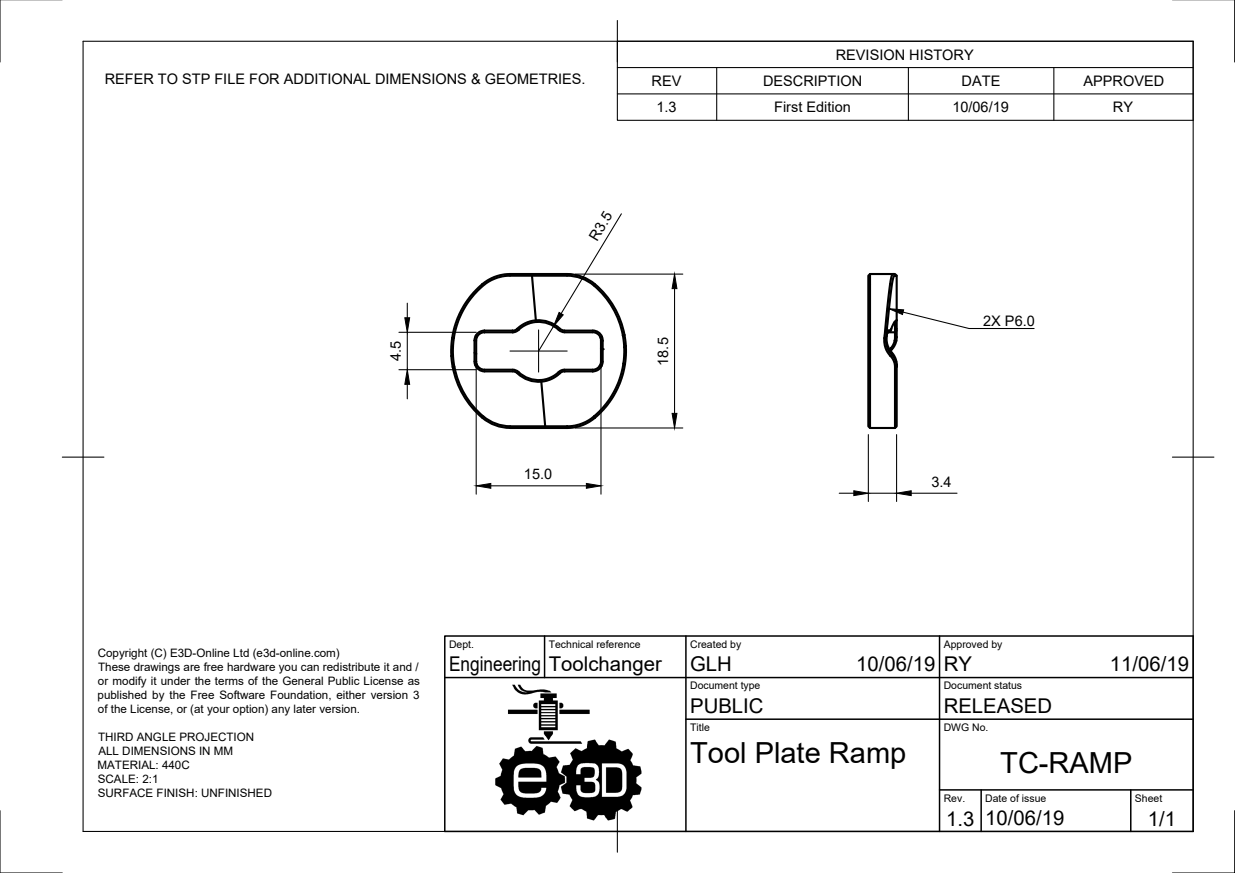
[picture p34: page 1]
REFER TO STP FILE FOR ADDITIONAL DIMENSIONS & GEOMETRIES.

REVISION HISTORY

REV | DESCRIPTION | DATE | APPROVED
1.3 | First Edition | 10/06/19 | RY

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

Dept. Engineering | Technical reference Toolchanger | Created by GLH 10/06/19 | Approved by RY 11/06/19

Document type PUBLIC | Document status RELEASED

of the License, or (at your option) any later version.

THIRD ANGLE PROJECTION
ALL DIMENSIONS IN MM
MATERIAL: 440C
SCALE: 2:1
SURFACE FINISH: UNFINISHED

Title | DWG No. TC-RAMP Tool Plate Ramp

Rev. 1.3 | Date of issue 10/06/19 | Sheet 1/1

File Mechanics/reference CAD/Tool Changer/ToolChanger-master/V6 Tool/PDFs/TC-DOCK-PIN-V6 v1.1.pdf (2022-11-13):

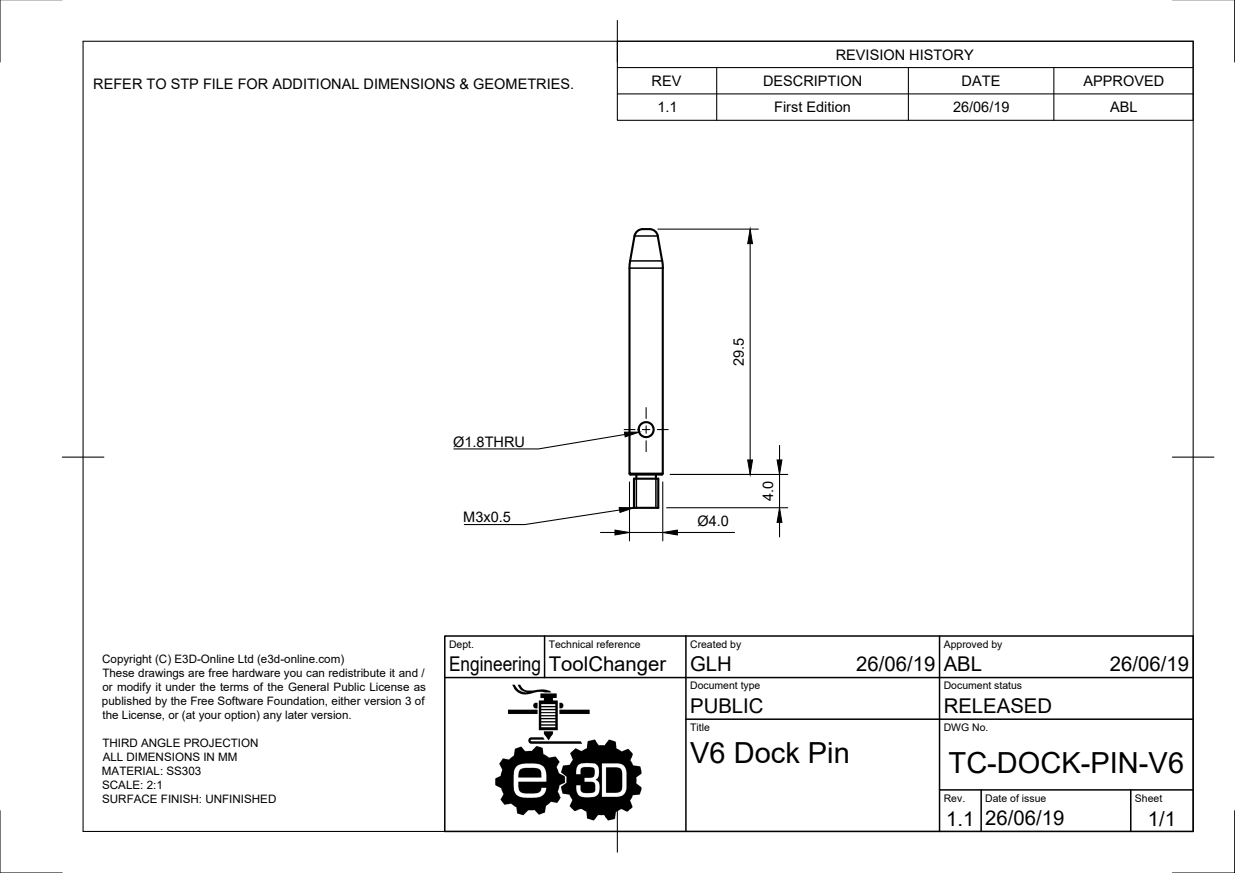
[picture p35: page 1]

REVISION HISTORY

REV | DESCRIPTION | DATE | APPROVED
1.1 | First Edition | 26/06/19 | ABL

REFER TO STP FILE FOR ADDITIONAL DIMENSIONS & GEOMETRIES.

Dept. Engineering | Technical reference ToolChanger | Created by GLH 26/06/19 | Approved by ABL 26/06/19

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

Document type PUBLIC | Document status RELEASED

the License, or (at your option) any later version.

Title | DWG No. TC-DOCK-PIN-V6 V6 Dock Pin

THIRD ANGLE PROJECTION
ALL DIMENSIONS IN MM
MATERIAL: SS303
SCALE: 2:1
SURFACE FINISH: UNFINISHED

Rev. 1.1 | Date of issue 26/06/19 | Sheet 1/1

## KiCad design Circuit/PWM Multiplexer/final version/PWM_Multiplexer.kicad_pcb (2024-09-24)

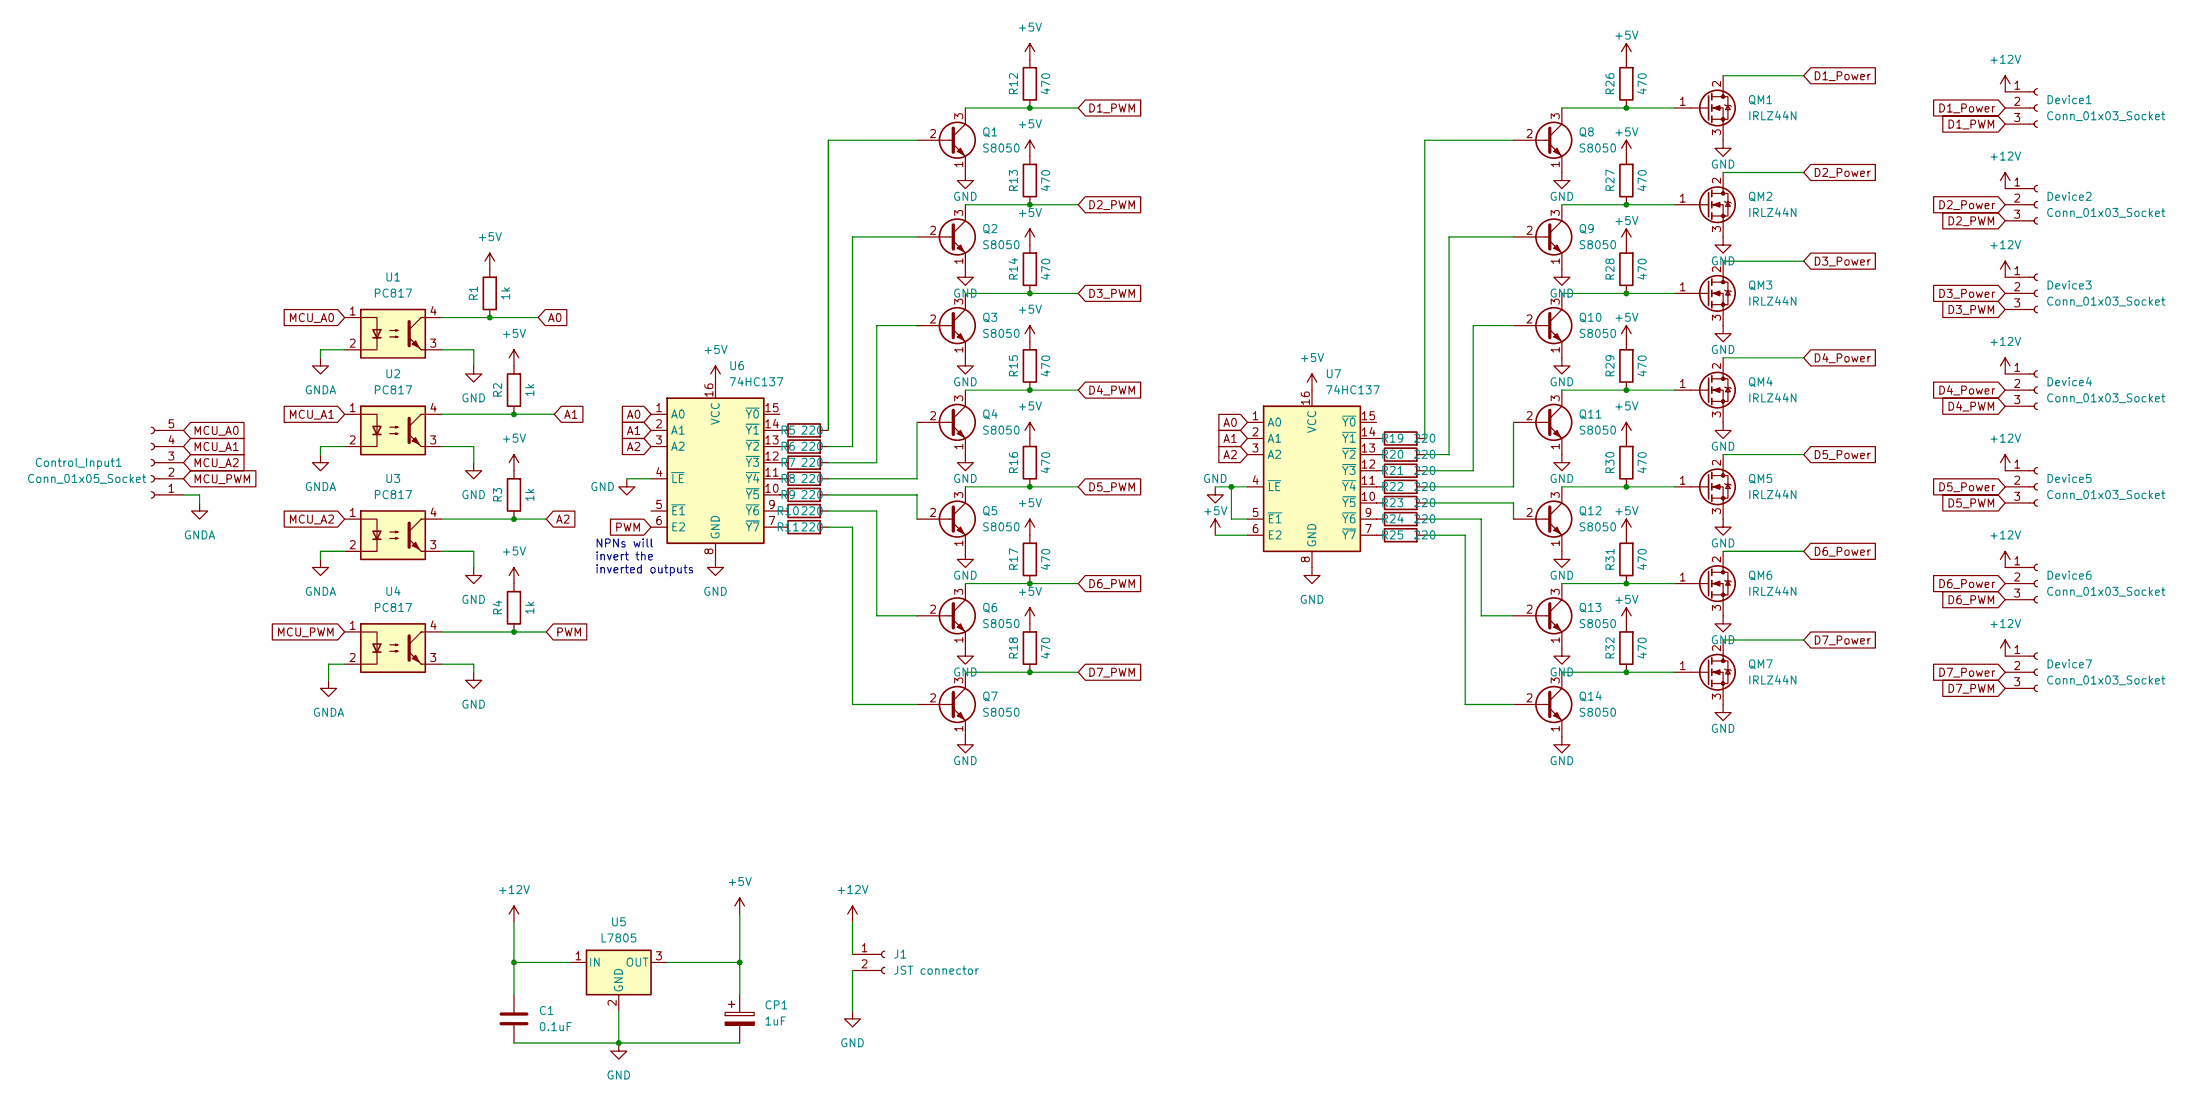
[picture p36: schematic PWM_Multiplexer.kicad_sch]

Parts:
C1: 0.1uF; C_Disc_D5.0mm_W2.5mm_P2.50mm
CP1: 1uF; CP_Radial_D5.0mm_P2.50mm
Control_Input1: Conn_01x05_Socket; JST_EH_S5B-EH_1x05_P2.50mm_Horizontal
Device1, Device2, Device3, Device4, Device5, Device6, Device7: Conn_01x03_Socket; JST_EH_S3B-EH_1x03_P2.50mm_Horizontal
J1: JST connector; JST_EH_S2B-EH_1x02_P2.50mm_Horizontal
Q1, Q2, Q3, Q4, Q5, Q6, Q7, Q8, Q9, Q10, Q11, Q12, Q13, Q14: S8050; TO-92_Inline
QM1, QM2, QM3, QM4, QM5, QM6, QM7: IRLZ44N; TO-220-3_Vertical
R1, R2, R3, R4: 1k; R_Axial_DIN0207_L6.3mm_D2.5mm_P7.62mm_Horizontal
R5, R6, R7, R8, R9, R10, R11: 220; R_Axial_DIN0207_L6.3mm_D2.5mm_P10.16mm_Horizontal
R12, R13, R14, R15, R16, R17, R18: 470; R_Axial_DIN0207_L6.3mm_D2.5mm_P7.62mm_Horizontal
R19, R20, R21, R22, R23, R24, R25: 220; R_Axial_DIN0207_L6.3mm_D2.5mm_P7.62mm_Horizontal
R26, R27, R28, R29, R30, R31, R32: 470; R_Axial_DIN0207_L6.3mm_D2.5mm_P10.16mm_Horizontal
U1, U2, U3, U4: PC817; DIP-4_W7.62mm
U5: L7805; TO-220-3_Vertical
U6, U7: 74HC137; DIP-16_W7.62mm_Socket_LongPads

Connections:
+5V: CP1.1, R1.2, R2.2, R3.2, R4.2, R12.2, R13.2, R14.2, R15.2, R16.2, R17.2, R18.2, R26.2, R27.2, R28.2, R29.2, R30.2, R31.2, R32.2, U5.3 (OUT), U6.16 (VCC), U7.6 (E2), U7.16 (VCC)
+12V: C1.1, Device1.1, Device2.1, Device3.1, Device4.1, Device5.1, Device6.1, Device7.1, J1.1, U5.1 (IN)
A0: R1.1, U1.4, U6.1 (A0), U7.1 (A0)
A1: R2.1, U2.4, U6.2 (A1), U7.2 (A1)
A2: R3.1, U3.4, U6.3 (A2), U7.3 (A2)
D1_PWM: Device1.3, Q1.3 (C), R12.1
D1_Power: Device1.2, QM1.2 (D)
D2_PWM: Device2.3, Q2.3 (C), R13.1
D2_Power: Device2.2, QM2.2 (D)
D3_PWM: Device3.3, Q3.3 (C), R14.1
D3_Power: Device3.2, QM3.2 (D)
D4_PWM: Device4.3, Q4.3 (C), R15.1
D4_Power: Device4.2, QM4.2 (D)
D5_PWM: Device5.3, Q5.3 (C), R16.1
D5_Power: Device5.2, QM5.2 (D)
D6_PWM: Device6.3, Q6.3 (C), R17.1
D6_Power: Device6.2, QM6.2 (D)
D7_PWM: Device7.3, Q7.3 (C), R18.1
D7_Power: Device7.2, QM7.2 (D)
GND: C1.2, CP1.2, J1.2, Q1.1 (E), Q2.1 (E), Q3.1 (E), Q4.1 (E), Q5.1 (E), Q6.1 (E), Q7.1 (E), Q8.1 (E), Q9.1 (E), Q10.1 (E), Q11.1 (E), Q12.1 (E), Q13.1 (E), Q14.1 (E), QM1.3 (S), QM2.3 (S), QM3.3 (S), QM4.3 (S), QM5.3 (S), QM6.3 (S), QM7.3 (S), U1.3, U2.3, U3.3, U4.3, U5.2 (GND), U6.4 (~LE), U6.8 (GND), U7.4 (~LE), U7.5 (~E1), U7.8 (GND)
GNDA: Control_Input1.1, U1.2, U2.2, U3.2, U4.2
MCU_A0: Control_Input1.5, U1.1
MCU_A1: Control_Input1.4, U2.1
MCU_A2: Control_Input1.3, U3.1
MCU_PWM: Control_Input1.2, U4.1
unnamed: Q1.2 (B), R5.2
unnamed: Q2.2 (B), R6.2
unnamed: Q3.2 (B), R7.2
unnamed: Q4.2 (B), R8.2
unnamed: Q5.2 (B), R9.2
unnamed: Q6.2 (B), R10.2
unnamed: Q7.2 (B), R11.2
unnamed: Q8.2 (B), R19.2
unnamed: Q8.3 (C), QM1.1 (G), R26.1
unnamed: Q9.2 (B), R20.2
unnamed: Q9.3 (C), QM2.1 (G), R27.1
unnamed: Q10.2 (B), R21.2
unnamed: Q10.3 (C), QM3.1 (G), R28.1
unnamed: Q11.2 (B), R22.2
unnamed: Q11.3 (C), QM4.1 (G), R29.1
unnamed: Q12.2 (B), R23.2
unnamed: Q12.3 (C), QM5.1 (G), R30.1
unnamed: Q13.2 (B), R24.2
unnamed: Q13.3 (C), QM6.1 (G), R31.1
unnamed: Q14.2 (B), R25.2
unnamed: Q14.3 (C), QM7.1 (G), R32.1
unnamed: R5.1, U6.14 (~Y1)
unnamed: R6.1, U6.13 (~Y2)
unnamed: R7.1, U6.12 (~Y3)
unnamed: R8.1, U6.11 (~Y4)
unnamed: R9.1, U6.10 (~Y5)
unnamed: R10.1, U6.9 (~Y6)
unnamed: R11.1, U6.7 (~Y7)
unnamed: R19.1, U7.14 (~Y1)
unnamed: R20.1, U7.13 (~Y2)
unnamed: R21.1, U7.12 (~Y3)
unnamed: R22.1, U7.11 (~Y4)
unnamed: R23.1, U7.10 (~Y5)
unnamed: R24.1, U7.9 (~Y6)
unnamed: R25.1, U7.7 (~Y7)
PWM: R4.1, U4.4, U6.6 (E2)

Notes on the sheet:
NPNs will invert the inverted outputs

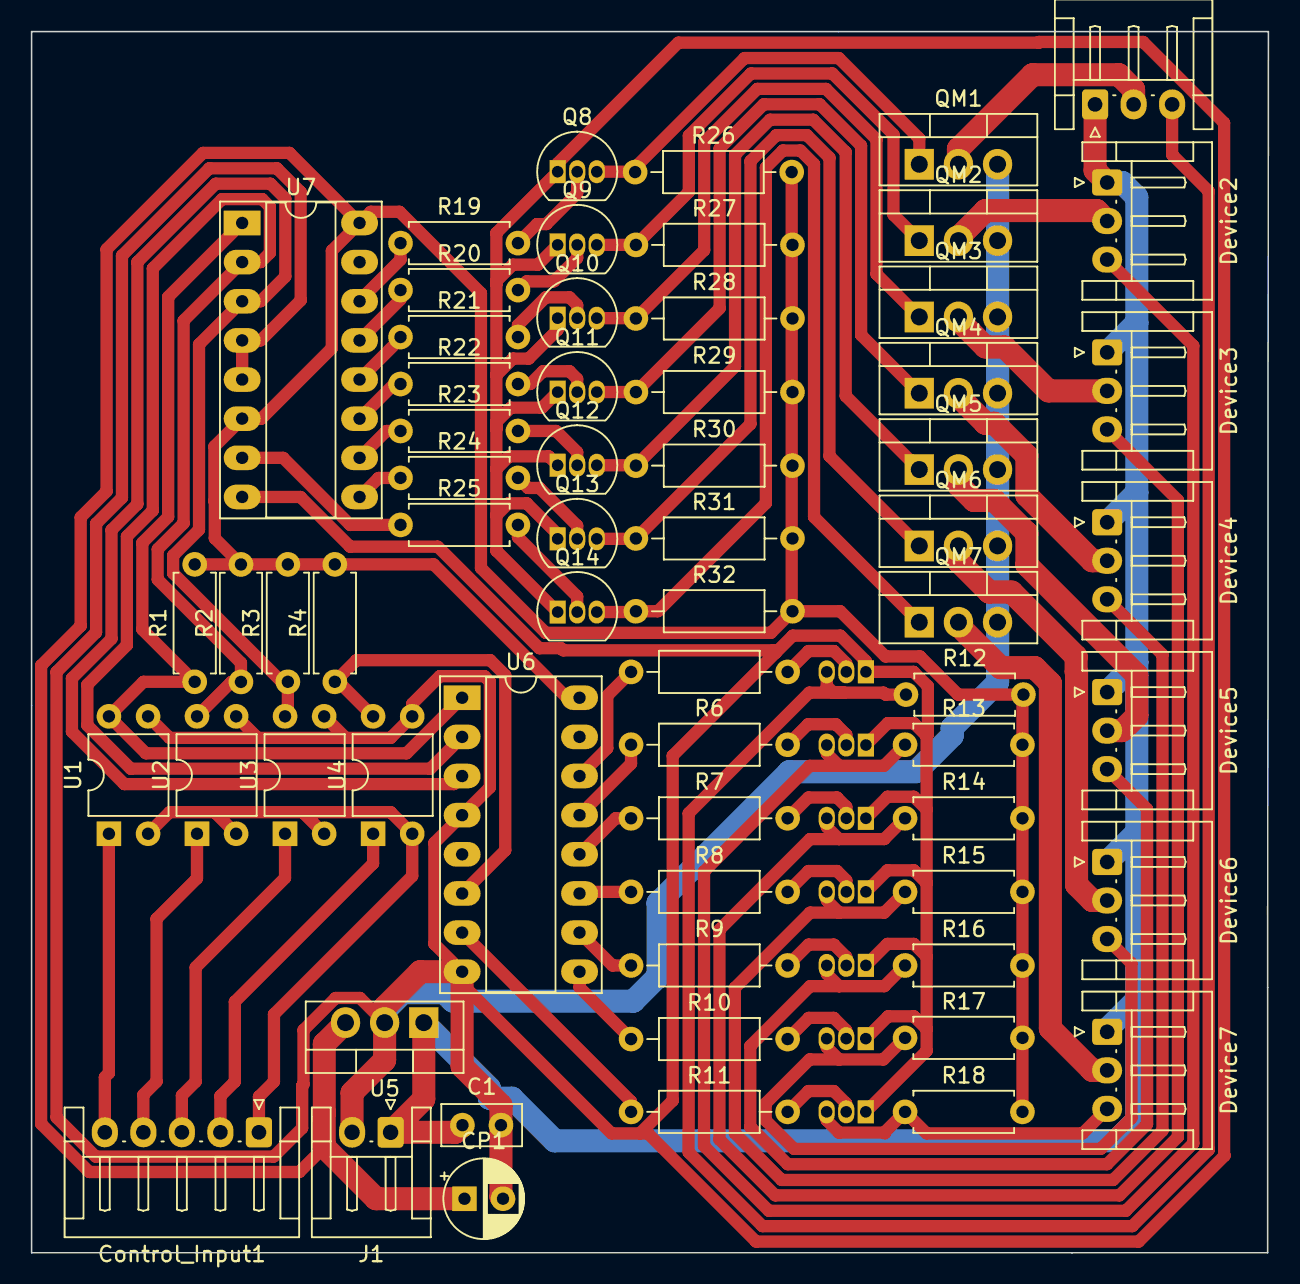
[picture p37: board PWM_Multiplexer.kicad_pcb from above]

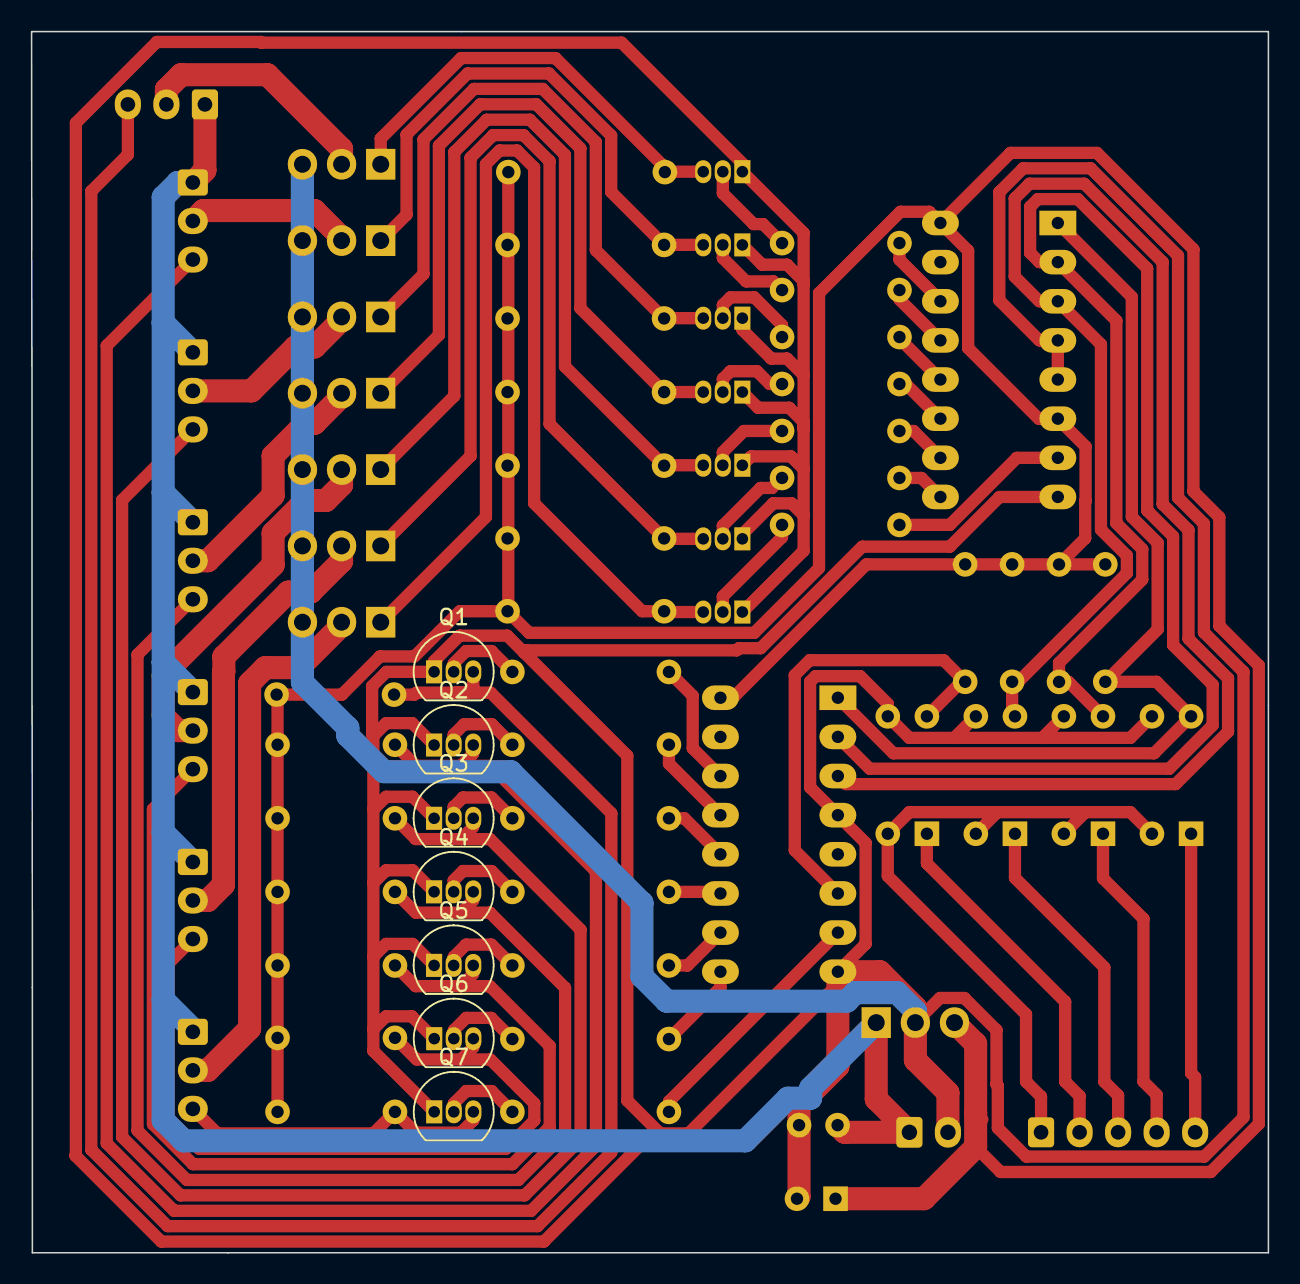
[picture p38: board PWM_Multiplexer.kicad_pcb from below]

Board: 2 copper layers, 80.3 x 79.2 mm, 71 parts (7 on the bottom side), 61 nets.

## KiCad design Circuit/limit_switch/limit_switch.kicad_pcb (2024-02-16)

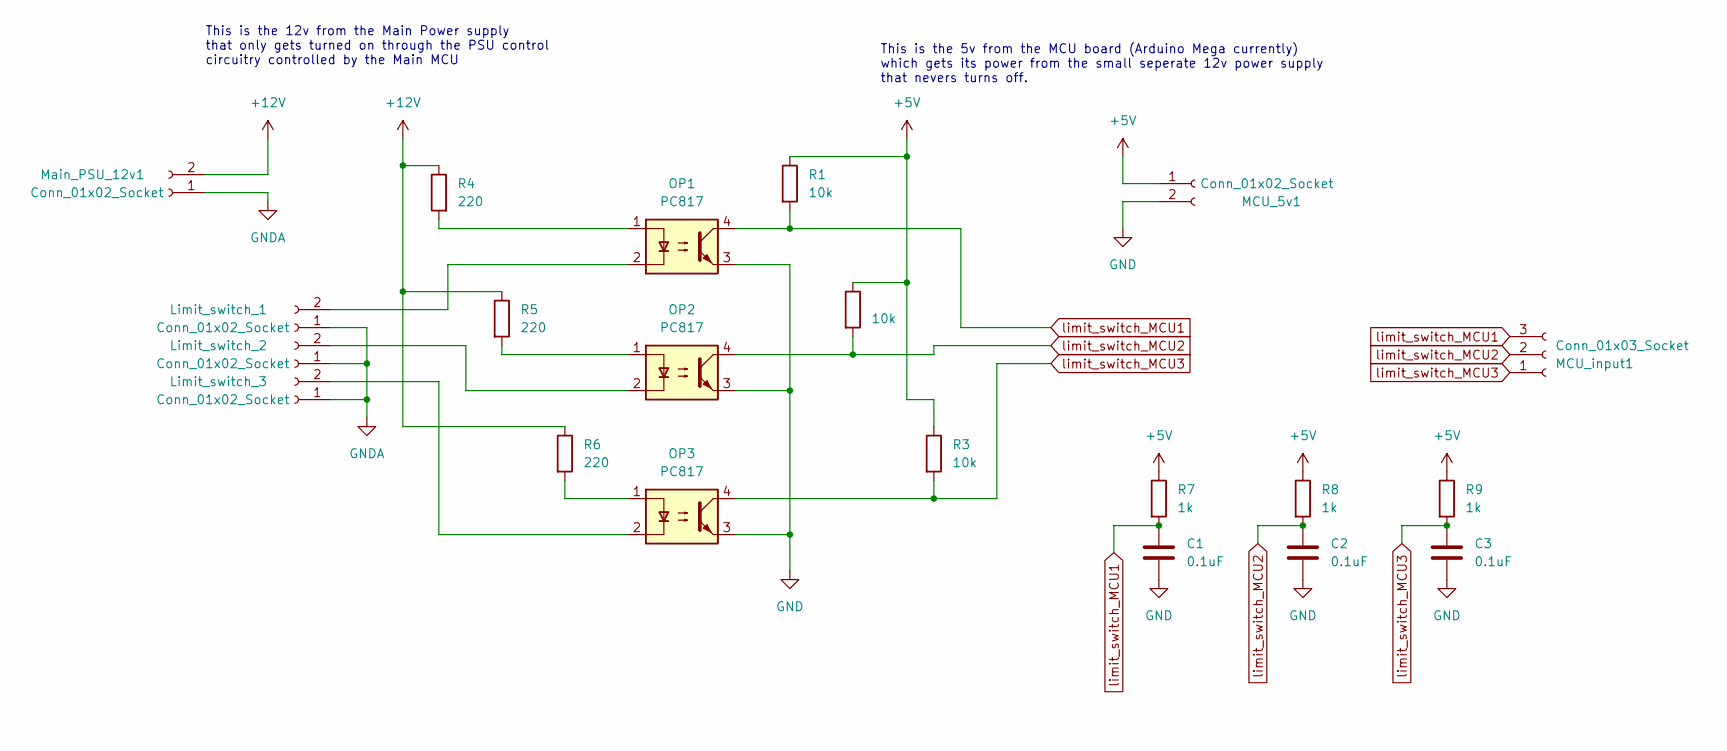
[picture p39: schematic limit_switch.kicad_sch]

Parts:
C1, C2, C3: 0.1uF; C_Disc_D5.0mm_W2.5mm_P5.00mm
Limit_switch_1, Limit_switch_2, Limit_switch_3: Conn_01x02_Socket; JST_EH_S2B-EH_1x02_P2.50mm_Horizontal
MCU_5v1: Conn_01x02_Socket; JST_EH_S2B-EH_1x02_P2.50mm_Horizontal
MCU_input1: Conn_01x03_Socket; JST_EH_S3B-EH_1x03_P2.50mm_Horizontal
Main_PSU_12v1: Conn_01x02_Socket; JST_EH_S2B-EH_1x02_P2.50mm_Horizontal
OP1, OP2, OP3: PC817; DIP-4_W7.62mm
R1, R2, R3: 10k; R_Axial_DIN0207_L6.3mm_D2.5mm_P7.62mm_Horizontal
R4, R5, R6: 220; R_Axial_DIN0207_L6.3mm_D2.5mm_P7.62mm_Horizontal
R7, R8, R9: 1k; R_Axial_DIN0207_L6.3mm_D2.5mm_P7.62mm_Horizontal

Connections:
+5V: MCU_5v1.1, R1.1, R2.1, R3.1, R7.1, R8.1, R9.1
+12V: Main_PSU_12v1.2, R4.1, R5.1, R6.1
GND: C1.2, C2.2, C3.2, MCU_5v1.2, OP1.3, OP2.3, OP3.3
GNDA: Limit_switch_1.1, Limit_switch_2.1, Limit_switch_3.1, Main_PSU_12v1.1
unnamed: Limit_switch_1.2, OP1.2
unnamed: Limit_switch_2.2, OP2.2
unnamed: Limit_switch_3.2, OP3.2
unnamed: OP1.1, R4.2
unnamed: OP2.1, R5.2
unnamed: OP3.1, R6.2
limit_switch_MCU1: C1.1, MCU_input1.3, OP1.4, R1.2, R7.2
limit_switch_MCU2: C2.1, MCU_input1.2, OP2.4, R2.2, R8.2
limit_switch_MCU3: C3.1, MCU_input1.1, OP3.4, R3.2, R9.2

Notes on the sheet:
This is the 12v from the Main Power supply that only gets turned on through the PSU control circuitry controlled by the Main MCU
This is the 5v from the MCU board (Arduino Mega currently) which gets its power from the small seperate 12v power supply that nevers turns off.

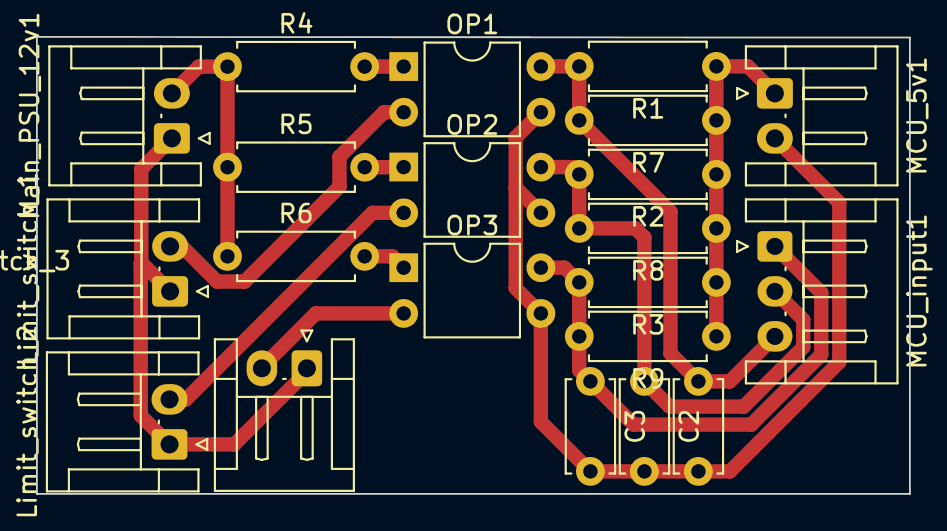
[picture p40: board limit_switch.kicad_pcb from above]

Board: 2 copper layers, 48.5 x 25.4 mm, 21 parts (0 on the bottom side), 13 nets.

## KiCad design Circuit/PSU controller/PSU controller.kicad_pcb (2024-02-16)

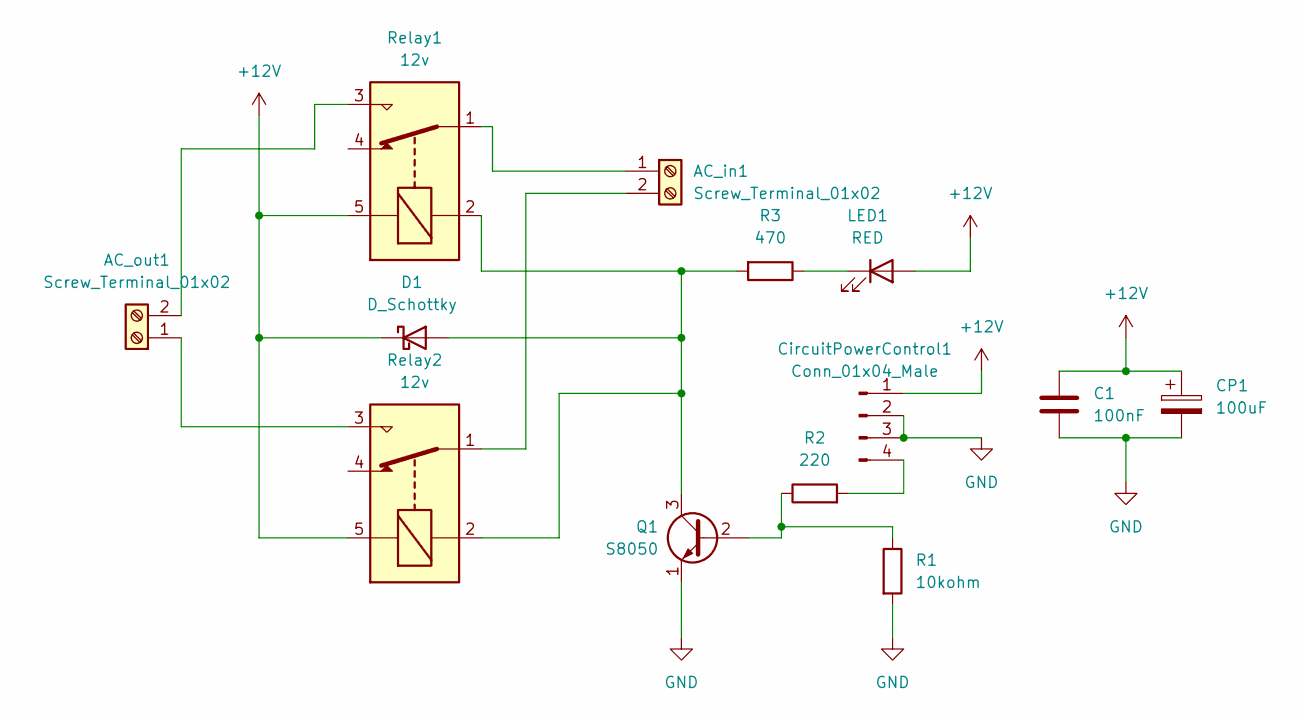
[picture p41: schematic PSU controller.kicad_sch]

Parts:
AC_in1: Screw_Terminal_01x02; TerminalBlock_bornier-2_P5.08mm
AC_out1: Screw_Terminal_01x02; TerminalBlock_bornier-2_P5.08mm
C1: 100nF; C_Disc_D5.0mm_W2.5mm_P2.50mm
CP1: 100uF; CP_Radial_D5.0mm_P2.00mm
CircuitPowerControl1: Conn_01x04_Male; PinSocket_1x04_P2.54mm_Vertical
D1: D_Schottky; D_DO-34_SOD68_P7.62mm_Horizontal
LED1: RED; D_A-405_P2.54mm_Vertical_AnodeUp
Q1: S8050; TO-92_Inline
R1: 10kohm; R_Axial_DIN0207_L6.3mm_D2.5mm_P7.62mm_Horizontal
R2: 220; R_Axial_DIN0207_L6.3mm_D2.5mm_P7.62mm_Horizontal
R3: 470; R_Axial_DIN0207_L6.3mm_D2.5mm_P7.62mm_Horizontal
Relay1, Relay2: 12v; Relay_SPDT_SANYOU_SRD_Series_Form_C

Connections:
+12V: C1.1, CP1.1, CircuitPowerControl1.1, D1.1 (K), LED1.2 (A), Relay1.5, Relay2.5
GND: C1.2, CP1.2, CircuitPowerControl1.2, CircuitPowerControl1.3, Q1.1 (E), R1.2
unnamed: AC_in1.1, Relay1.1
unnamed: AC_in1.2, Relay2.1
unnamed: AC_out1.1, Relay2.3
unnamed: AC_out1.2, Relay1.3
unnamed: CircuitPowerControl1.4, R2.2
unnamed: D1.2 (A), Q1.3 (C), R3.2, Relay1.2, Relay2.2
unnamed: LED1.1 (K), R3.1
unnamed: Q1.2 (B), R1.1, R2.1

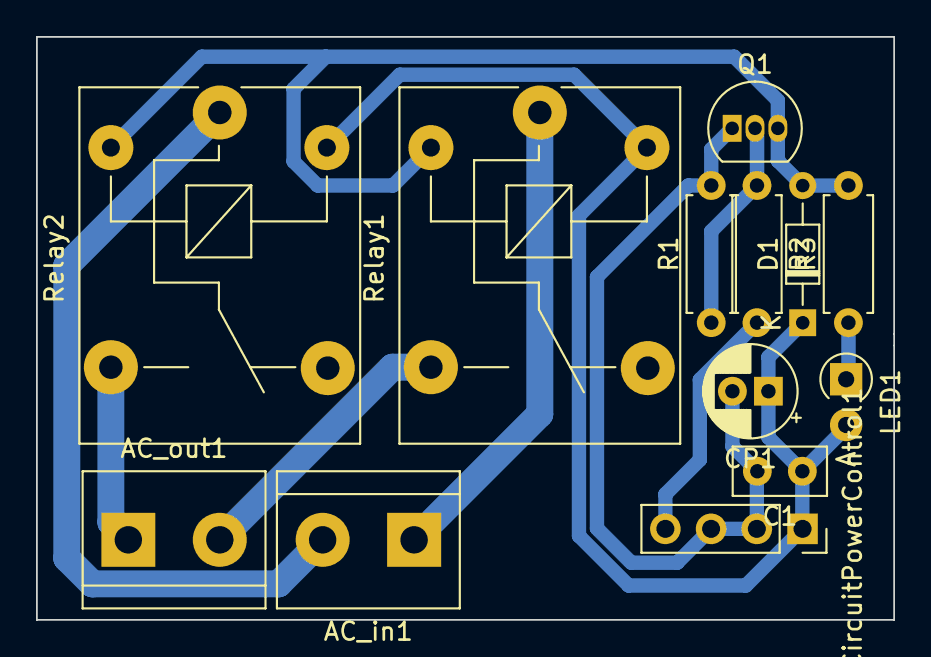
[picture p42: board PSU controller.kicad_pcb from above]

Board: 2 copper layers, 47.6 x 32.4 mm, 13 parts (0 on the bottom side), 10 nets.

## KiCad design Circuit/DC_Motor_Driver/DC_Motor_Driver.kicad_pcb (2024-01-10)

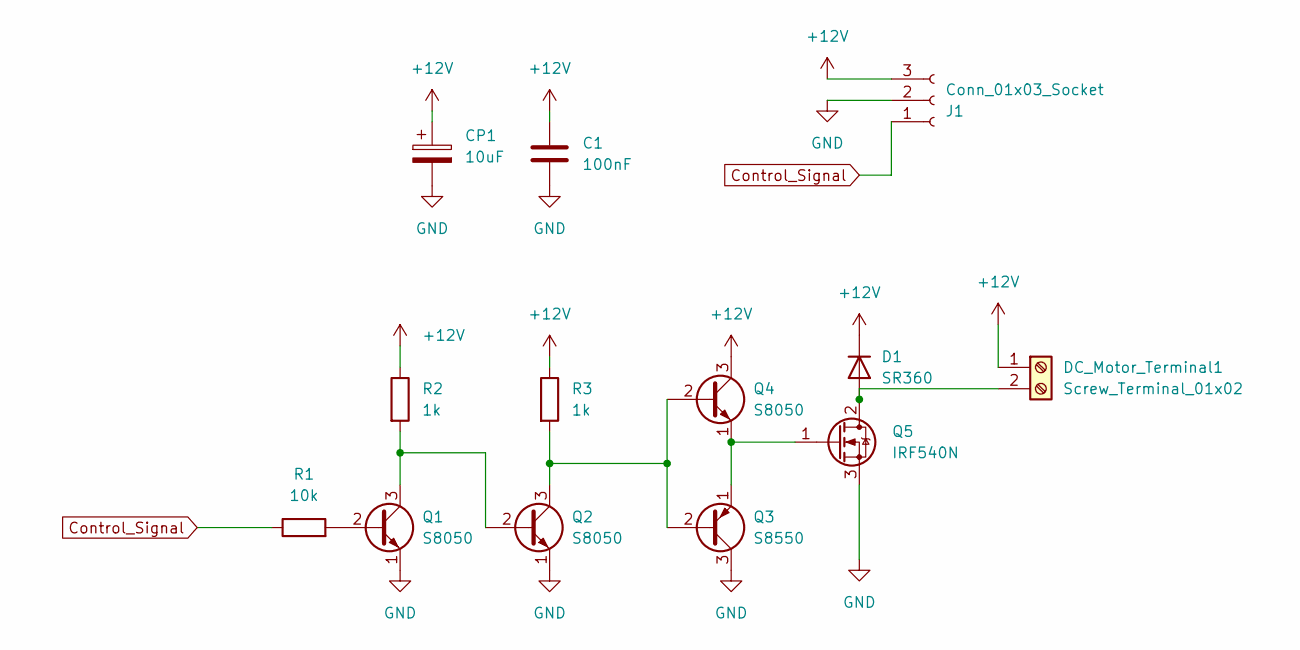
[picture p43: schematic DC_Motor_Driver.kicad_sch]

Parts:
C1: 100nF; C_Disc_D5.0mm_W2.5mm_P2.50mm
CP1: 10uF; CP_Radial_D5.0mm_P2.50mm
D1: SR360; D_DO-27_P12.70mm_Horizontal
DC_Motor_Terminal1: Screw_Terminal_01x02; TerminalBlock_bornier-2_P5.08mm
J1: Conn_01x03_Socket; JST_EH_S3B-EH_1x03_P2.50mm_Horizontal
Q1, Q2, Q4: S8050; TO-92_Inline
Q3: S8550; TO-92_Inline
Q5: IRF540N; TO-220-3_Vertical
R1: 10k; R_Axial_DIN0207_L6.3mm_D2.5mm_P7.62mm_Horizontal
R2, R3: 1k; R_Axial_DIN0207_L6.3mm_D2.5mm_P7.62mm_Horizontal

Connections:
+12V: C1.1, CP1.1, D1.1 (K), DC_Motor_Terminal1.1, J1.3, Q4.3 (C), R2.1, R3.1
Control_Signal: J1.1, R1.1
GND: C1.2, CP1.2, J1.2, Q1.1 (E), Q2.1 (E), Q3.3 (C), Q5.3 (S)
unnamed: D1.2 (A), DC_Motor_Terminal1.2, Q5.2 (D)
unnamed: Q1.2 (B), R1.2
unnamed: Q1.3 (C), Q2.2 (B), R2.2
unnamed: Q2.3 (C), Q3.2 (B), Q4.2 (B), R3.2
unnamed: Q3.1 (E), Q4.1 (E), Q5.1 (G)

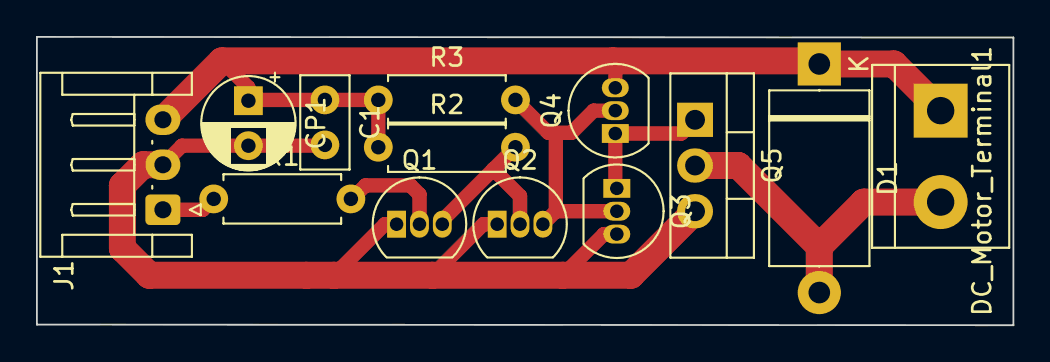
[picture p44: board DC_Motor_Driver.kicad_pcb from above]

Board: 2 copper layers, 54.2 x 16.0 mm, 13 parts (0 on the bottom side), 8 nets.

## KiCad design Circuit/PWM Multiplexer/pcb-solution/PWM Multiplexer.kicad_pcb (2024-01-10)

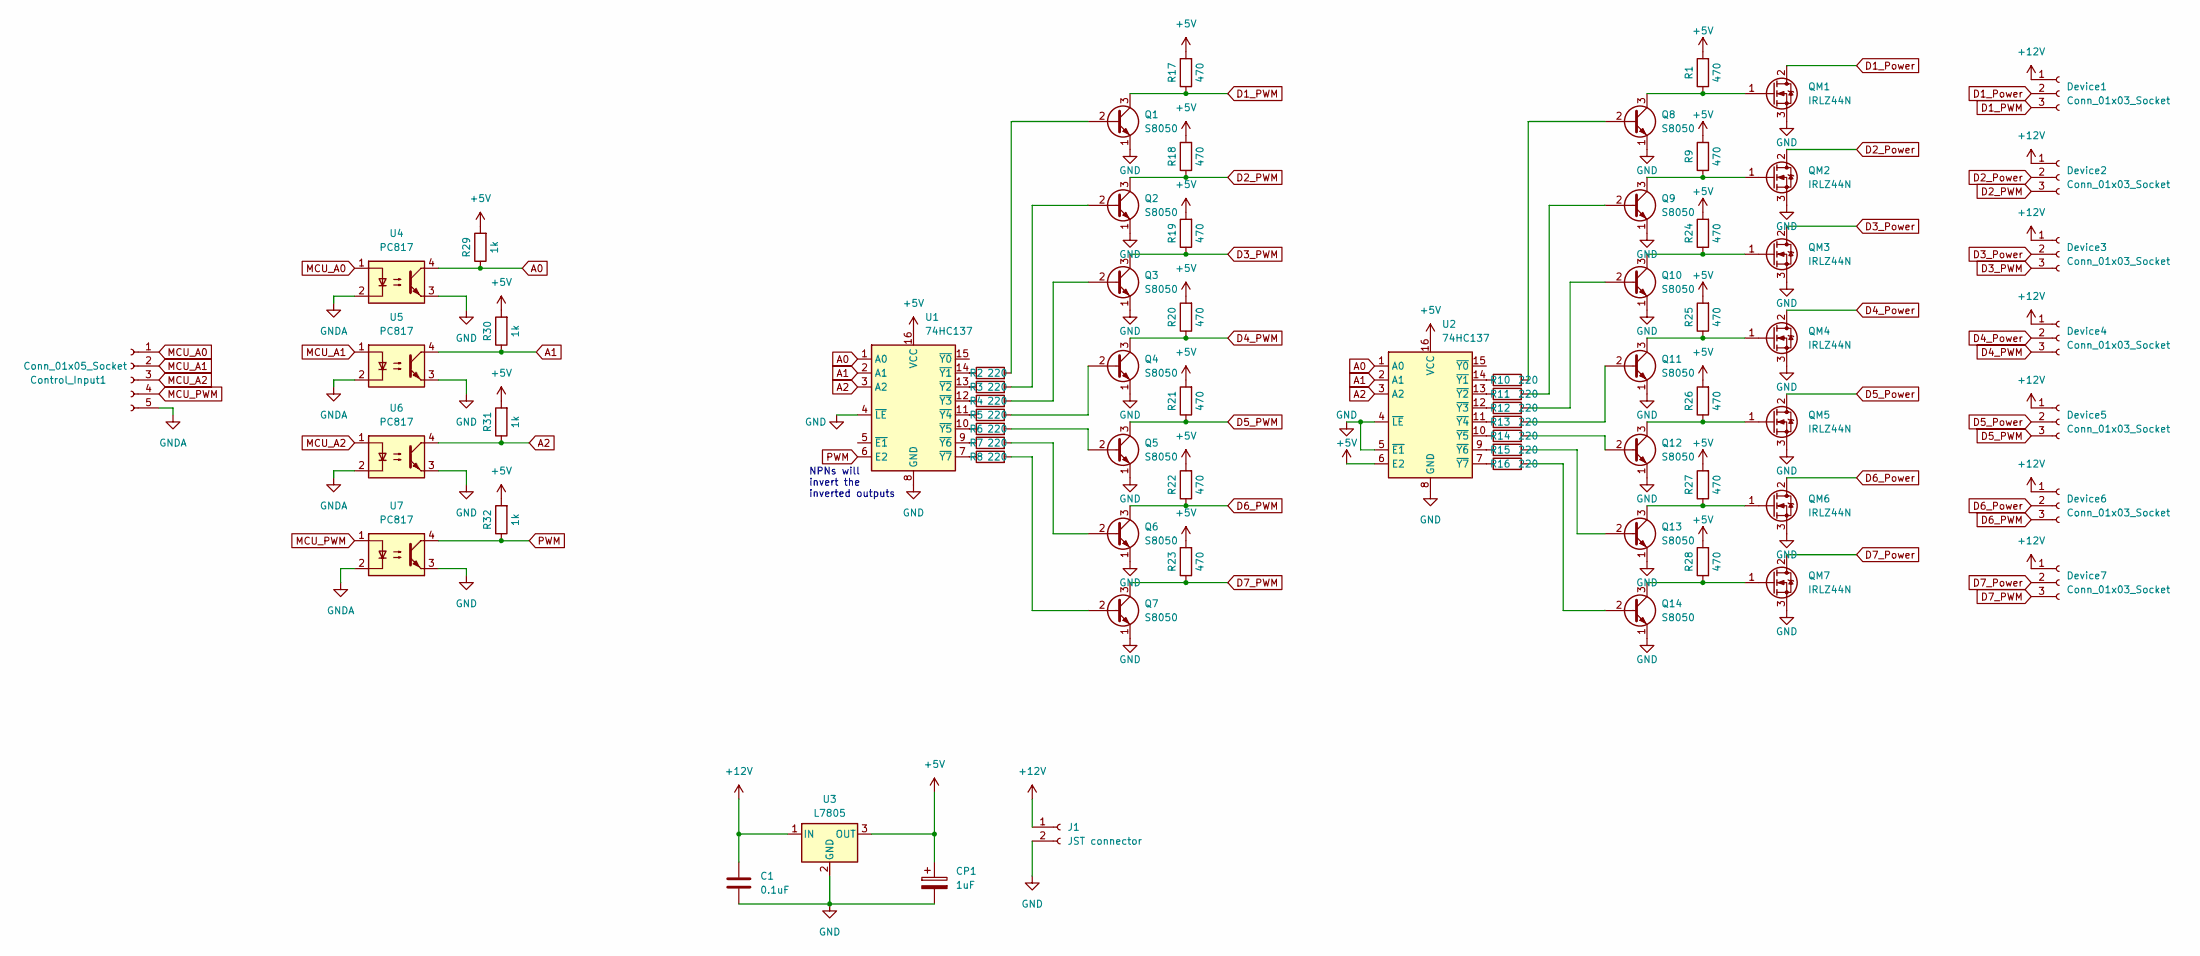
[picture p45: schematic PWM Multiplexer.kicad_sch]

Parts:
C1: 0.1uF; C_Disc_D5.0mm_W2.5mm_P2.50mm
CP1: 1uF; CP_Radial_D5.0mm_P2.50mm
Control_Input1: Conn_01x05_Socket; PinSocket_1x05_P2.54mm_Horizontal
Device1, Device2, Device3, Device4, Device5, Device6, Device7: Conn_01x03_Socket; PinSocket_1x03_P2.54mm_Horizontal
J1: JST connector; JST_EH_S2B-EH_1x02_P2.50mm_Horizontal
Q1, Q2, Q3, Q4, Q5, Q6, Q7, Q8, Q9, Q10, Q11, Q12, Q13, Q14: S8050; TO-92_Inline
QM1, QM2, QM3, QM4, QM5, QM6, QM7: IRLZ44N; TO-220-3_Vertical
R1, R9, R17, R18, R19, R20, R21, R22, R23, R24, R25, R26, R27, R28: 470; R_Axial_DIN0207_L6.3mm_D2.5mm_P10.16mm_Horizontal
R2, R3, R4, R5, R6, R7, R8, R10, R11, R12, R13, R14, R15, R16: 220; R_Axial_DIN0207_L6.3mm_D2.5mm_P7.62mm_Horizontal
R29, R30, R31, R32: 1k; R_Axial_DIN0207_L6.3mm_D2.5mm_P10.16mm_Horizontal
U1, U2: 74HC137; DIP-16_W7.62mm_Socket_LongPads
U3: L7805; TO-220-3_Vertical
U4, U5, U6, U7: PC817; DIP-4_W7.62mm

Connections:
+5V: CP1.1, R1.2, R9.2, R17.2, R18.2, R19.2, R20.2, R21.2, R22.2, R23.2, R24.2, R25.2, R26.2, R27.2, R28.2, R29.2, R30.2, R31.2, R32.2, U1.16 (VCC), U2.6 (E2), U2.16 (VCC), U3.3 (OUT)
+12V: C1.1, Device1.1, Device2.1, Device3.1, Device4.1, Device5.1, Device6.1, Device7.1, J1.1, U3.1 (IN)
A0: R29.1, U1.1 (A0), U2.1 (A0), U4.4
A1: R30.1, U1.2 (A1), U2.2 (A1), U5.4
A2: R31.1, U1.3 (A2), U2.3 (A2), U6.4
D1_PWM: Device1.3, Q1.3 (C), R17.1
D1_Power: Device1.2, QM1.2 (D)
D2_PWM: Device2.3, Q2.3 (C), R18.1
D2_Power: Device2.2, QM2.2 (D)
D3_PWM: Device3.3, Q3.3 (C), R19.1
D3_Power: Device3.2, QM3.2 (D)
D4_PWM: Device4.3, Q4.3 (C), R20.1
D4_Power: Device4.2, QM4.2 (D)
D5_PWM: Device5.3, Q5.3 (C), R21.1
D5_Power: Device5.2, QM5.2 (D)
D6_PWM: Device6.3, Q6.3 (C), R22.1
D6_Power: Device6.2, QM6.2 (D)
D7_PWM: Device7.3, Q7.3 (C), R23.1
D7_Power: Device7.2, QM7.2 (D)
GND: C1.2, CP1.2, J1.2, Q1.1 (E), Q2.1 (E), Q3.1 (E), Q4.1 (E), Q5.1 (E), Q6.1 (E), Q7.1 (E), Q8.1 (E), Q9.1 (E), Q10.1 (E), Q11.1 (E), Q12.1 (E), Q13.1 (E), Q14.1 (E), QM1.3 (S), QM2.3 (S), QM3.3 (S), QM4.3 (S), QM5.3 (S), QM6.3 (S), QM7.3 (S), U1.4 (~LE), U1.8 (GND), U2.4 (~LE), U2.5 (~E1), U2.8 (GND), U3.2 (GND), U4.3, U5.3, U6.3, U7.3
GNDA: Control_Input1.5, U4.2, U5.2, U6.2, U7.2
MCU_A0: Control_Input1.1, U4.1
MCU_A1: Control_Input1.2, U5.1
MCU_A2: Control_Input1.3, U6.1
MCU_PWM: Control_Input1.4, U7.1
unnamed: Q1.2 (B), R2.2
unnamed: Q2.2 (B), R3.2
unnamed: Q3.2 (B), R4.2
unnamed: Q4.2 (B), R5.2
unnamed: Q5.2 (B), R6.2
unnamed: Q6.2 (B), R7.2
unnamed: Q7.2 (B), R8.2
unnamed: Q8.2 (B), R10.2
unnamed: Q8.3 (C), QM1.1 (G), R1.1
unnamed: Q9.2 (B), R11.2
unnamed: Q9.3 (C), QM2.1 (G), R9.1
unnamed: Q10.2 (B), R12.2
unnamed: Q10.3 (C), QM3.1 (G), R24.1
unnamed: Q11.2 (B), R13.2
unnamed: Q11.3 (C), QM4.1 (G), R25.1
unnamed: Q12.2 (B), R14.2
unnamed: Q12.3 (C), QM5.1 (G), R26.1
unnamed: Q13.2 (B), R15.2
unnamed: Q13.3 (C), QM6.1 (G), R27.1
unnamed: Q14.2 (B), R16.2
unnamed: Q14.3 (C), QM7.1 (G), R28.1
unnamed: R2.1, U1.14 (~Y1)
unnamed: R3.1, U1.13 (~Y2)
unnamed: R4.1, U1.12 (~Y3)
unnamed: R5.1, U1.11 (~Y4)
unnamed: R6.1, U1.10 (~Y5)
unnamed: R7.1, U1.9 (~Y6)
unnamed: R8.1, U1.7 (~Y7)
unnamed: R10.1, U2.14 (~Y1)
unnamed: R11.1, U2.13 (~Y2)
unnamed: R12.1, U2.12 (~Y3)
unnamed: R13.1, U2.11 (~Y4)
unnamed: R14.1, U2.10 (~Y5)
unnamed: R15.1, U2.9 (~Y6)
unnamed: R16.1, U2.7 (~Y7)
PWM: R32.1, U1.6 (E2), U7.4

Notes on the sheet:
NPNs will invert the inverted outputs

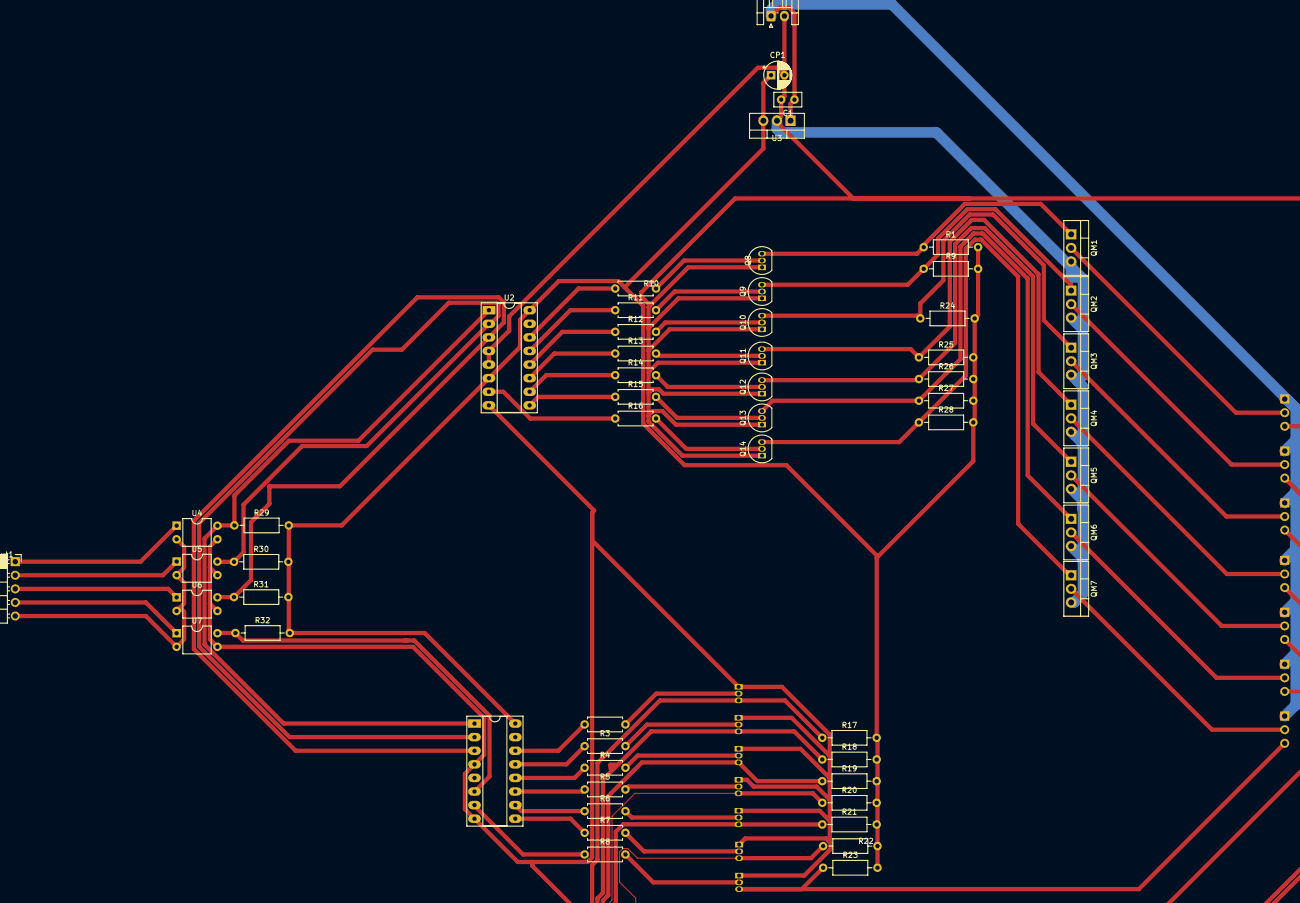
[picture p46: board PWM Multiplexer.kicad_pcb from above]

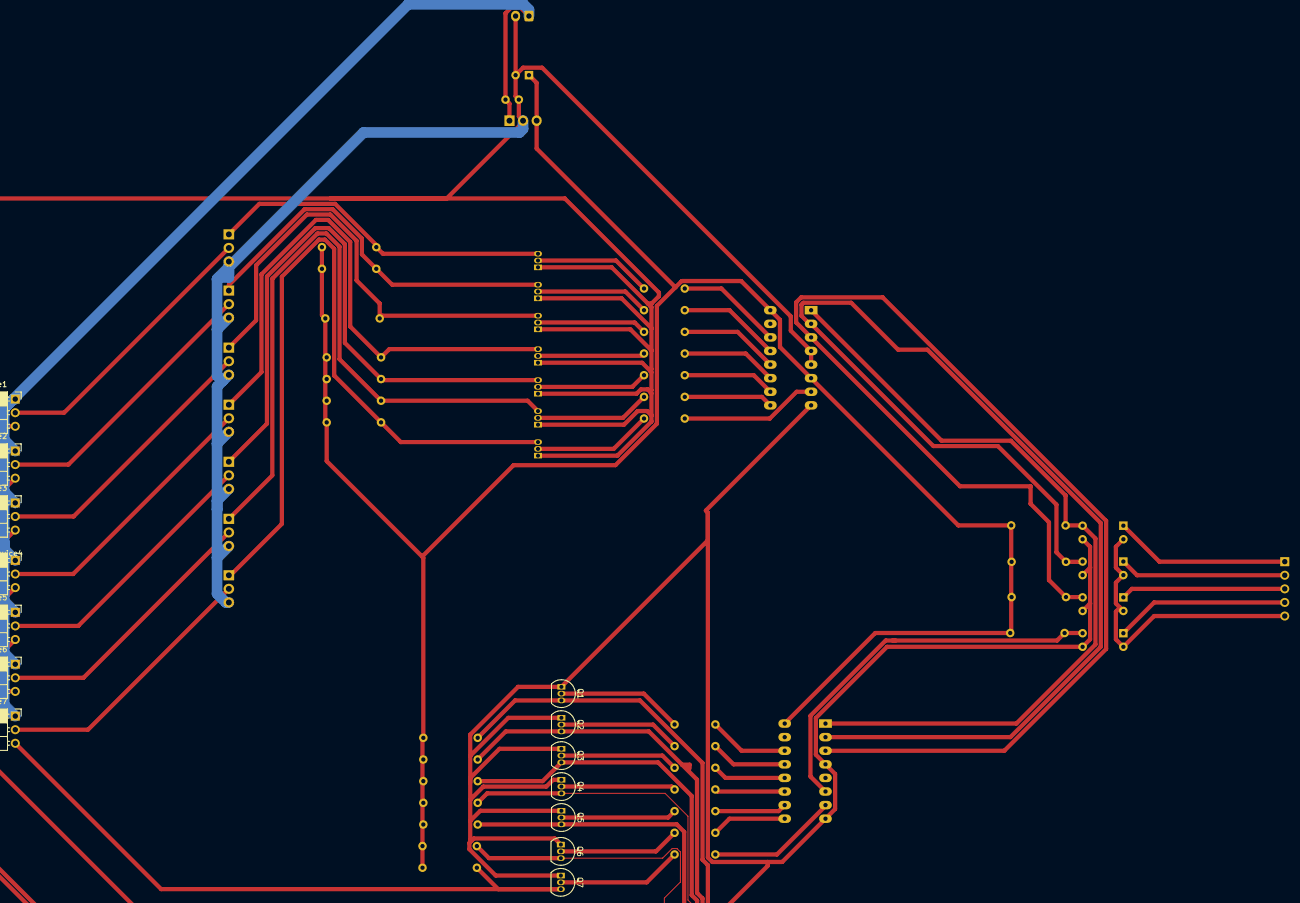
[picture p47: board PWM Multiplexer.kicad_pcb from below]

Board: 2 copper layers, 71 parts (14 on the bottom side), 61 nets.

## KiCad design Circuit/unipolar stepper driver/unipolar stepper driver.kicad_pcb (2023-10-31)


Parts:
C1: 10nF; C_Disc_D3.0mm_W2.0mm_P2.50mm
CP1: C_Polarized; CP_Radial_D5.0mm_P2.50mm
D1, D2, D3, D4: 1N5817; D_DO-34_SOD68_P7.62mm_Horizontal
Debug/UART_pin1: Conn_01x01_Socket; PinSocket_1x01_P2.54mm_Vertical
DebuggerPins1: Conn_01x05_Female; PinHeader_1x05_P2.54mm_Vertical
Input1: Conn_01x03_Female; PinHeader_1x03_P2.54mm_Vertical
Output1: Conn_01x05_Female; PinHeader_1x05_P2.54mm_Vertical
PowerRegulator1: LM7805_TO220; TO-220-3_Vertical
Q1, Q2, Q3, Q4: S8050; TO-92_Inline
R1, R2, R3, R4: 330; R_Axial_DIN0207_L6.3mm_D2.5mm_P7.62mm_Horizontal
R5: 10k; R_Axial_DIN0207_L6.3mm_D2.5mm_P7.62mm_Horizontal
uC1: PIC12F675-IP; DIP-8_W7.62mm

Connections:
+5V: C1.2, CP1.1, D1.1 (K), D2.1 (K), D3.1 (K), D4.1 (K), DebuggerPins1.2, Output1.1, PowerRegulator1.3 (VO), uC1.1 (VDD)
+12V: Input1.2, PowerRegulator1.1 (VI)
Coil_1: DebuggerPins1.4, R1.1, uC1.7 (GP0)
Coil_2: DebuggerPins1.5, R2.1, uC1.6 (GP1)
Coil_3: R3.1, uC1.5 (GP2)
Coil_4: R4.1, uC1.3 (GP4)
Control_Input: DebuggerPins1.1, Input1.3, R5.2, uC1.4 (GP3)
Debug/UART pin: Debug/UART_pin1.1, uC1.2 (GP5)
GND: C1.1, CP1.2, DebuggerPins1.3, Input1.1, PowerRegulator1.2 (GND), Q1.1 (E), Q2.1 (E), Q3.1 (E), Q4.1 (E), R5.1, uC1.8 (VSS)
unnamed: D1.2 (A), Output1.3, Q3.3 (C)
unnamed: D2.2 (A), Output1.4, Q2.3 (C)
unnamed: D3.2 (A), Output1.2, Q4.3 (C)
unnamed: D4.2 (A), Output1.5, Q1.3 (C)
unnamed: Q1.2 (B), R1.2
unnamed: Q2.2 (B), R2.2
unnamed: Q3.2 (B), R3.2
unnamed: Q4.2 (B), R4.2

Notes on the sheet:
red wire is Vcc orange wire is GPIO4, 4th npn, closest to Vcc(red wire) blue wire is GPIO0, 1st npn, farthest from Vcc(red wire


Board: 2 copper layers, 52.1 x 28.2 mm, 21 parts (0 on the bottom side), 17 nets.

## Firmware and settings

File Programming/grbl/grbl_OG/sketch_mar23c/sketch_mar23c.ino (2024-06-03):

#define IN1_2 48
#define IN2_2 49
#define ENA_2 11

void setup() {
  // put your setup code here, to run once:
  /****** Motor 2 setup ******/
  pinMode(IN1_2, OUTPUT);
  pinMode(IN2_2, OUTPUT);
  pinMode(ENA_2, OUTPUT);

}

void loop() {
  // put your main code here, to run repeatedly:
    digitalWrite(IN1_2, HIGH);
    digitalWrite(IN2_2, LOW);
  analogWrite(ENA_2, 200);
}

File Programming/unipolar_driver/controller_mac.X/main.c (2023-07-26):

/*
 * File:   main.c
 * Author: AbdulRahman
 *
 * Created on October 30, 2022, 7:31 PM
 */


#include "includes.h"

void main(void) {
    
    // INITs/DEINITs
    coil_init();
    comparator_deinit();
    interrupt_init();
    TMR1_init();
    adc_deinit();
#ifdef ENABLE_SOFT_UART
    soft_uart_init();
#endif
    
    // Initial Pin Setup
    reset_all_pins();
    
    // Initial delay
    __delay_ms(2000); // waiting for voltage to stabilize
    retrieve_current_position();
    
    // Main Routine
    while(1) {
        
        if(INPUT != CW_CCW_select) {
            CW_CCW_select = INPUT;
            start_timer();
        }
        
#ifdef ENABLE_SOFT_UART

//        soft_uart_send_ALL();
        soft_uart_send_int_AS_IS(current_position);
   
        __delay_ms(5);
#endif
        
    }
    
    return;
}


void __interrupt() ISR(void) {
    
    if(TMR1IF) {
        TMR1_ISR();
        TMR1IF = 0;
        
    }
    
    return;
    
}

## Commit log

2022-11-08 Fixed Merge conflict
    [Export.3mf, Hemera Bowden Bracket.step, Hemera Bowden Bracket.stl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]
2022-11-13 First Windows Commit
    [Export.3mf, Male.3mf, Nema 17 holes Spacer.stl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]
2022-11-20 Added grbl for Arduino Uno files for testing
    [config.h, cpu_map.h, defaults.h]
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2022-11-22 Renamed and rearranged Programming folders
    [alarm_codes_en_US.csv, build_option_codes_en_US.csv, config.h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]
2022-11-24 Corrected file structure to work with arduino
    [error_codes_en_US.csv]
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2022-11-30 ADDED LATCH COMMAND to grbl files
    [PWM Multiplexer.kicad_pcb, PWM Multiplexer.kicad_sch]
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2022-12-14 Modified unipolar driver code and PWM multiplexer circuit
    [PWM Multiplexer.kicad_sch]
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2022-12-18 Modified unipolar driver circuit and generated outputs
    [unipolar stepper driver-F_Cu.dxf, unipolar stepper driver.kicad_pcb, unipolar stepper driver.kicad_sch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]
2022-12-18 created gerber files for unipolar circuit
    [unipolar stepper driver.kicad_pcb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]
2022-12-18 Modified unipolar gerber file
    [unipolar stepper driver.kicad_pcb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]
2022-12-25 Added PSU control Circuit
    [PCU controller.kicad_pcb, PCU controller.kicad_sch, unipolar stepper driver-F_Cu.dxf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]
2022-12-25 Added DXF files for PSU controller circuit
    [PSU controller-B_Cu.dxf, PSU controller-B_Mask.dxf, PSU controller-B_Paste.dxf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]
2022-12-25 Added Gerber files for PSU controller
    [PSU controller.kicad_pcb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]
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2022-12-27 Created Unipolar Stepper PCB design
    [unipolar stepper driver.kicad_pcb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]
2022-12-27 Started DC Motor Driver Circuit schematic
    [DC Motor Driver.kicad_pcb, DC Motor Driver.kicad_sch]
2022-12-28 Modified PSU controller circuit
    [PSU controller.kicad_pcb, PSU controller.kicad_sch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]
2022-12-30 Finished DC Motor Driver Circuit, Schematic Design, testing and PCB design
    [DC Motor Driver.kicad_pcb, DC Motor Driver.kicad_sch, DC_Motor_Driver.kicad_pcb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]
2023-01-05 Finished PCB hole CAM module
    [PSU controller-F_Cu.gbr, PSU controller-NPTH-drl-drl_map.gbr, PSU controller-NPTH-drl.gbr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]
2023-01-21 started limit switch circuit development
    [limit_switch.kicad_pcb, limit_switch.kicad_sch]
2023-01-31 Developing limit switch circuit
    [limit_switch.kicad_pcb, limit_switch.kicad_sch]
2023-02-15 Fixing the random movement unipolar driver bug
    [cpu_map.h]
2023-02-16 further attempt at fixing unipolar driver bug
    [cpu_map.h]
2023-02-19 Finally Fixed Unipolar driver bug
    [main.c, software_uart.c, tmr1_module.c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]
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2023-02-23 Debugging limit switch high distance travel problem
2023-02-23 further trials to solve limit switch high distance problem
2023-02-23 further debugging of limit switch problem
2023-02-23 Added Description of homing_pull_off problem in limits.c
2023-02-23 Final change in limit switch problem saga
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2023-03-06 Finished developing ink-laying gcode gernator and made progress in creating the tcp-to-uart bridge on esp8266
    [all.gbr, default.gbr, test.gbr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]
2023-03-12 Fixed extract block bug and started implementing laser gcode generator
    [gcode_tools.py]
2023-03-20 Finished gerber_tools.py OOP development
    [test2.gbr]
2023-03-20 Integrated new OOP code with 'main.py' and 'gcode_tools.py'
    [test2.gbr]
2023-03-20 Fixed Stupid coordinate variable copying bug
    [test2.gbr]
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2023-03-25 Fixed Graph.sererate() and started DP for getting continious round-trip trace track
2023-04-03 Another huge patch of bug fixes for Edge.apply_offsets(new corner cases)
    [gcode_tools.py]
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2023-04-08 Fixed missing semicircle coords problem
    [gcode_tools.py]
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2023-04-16 Started implementing .incorporate_componentpads() and .point_edge_intersection()
    [dump.txt]
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2023-04-28 Bug fixes for previous commit
    [gcode_tools.py]
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2023-05-10 .add_comppad() works on default.gbr not test2.gbr
    [edge_cut.gbr, test1b.gbr, test1c.gbr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]
2023-05-25 Finished generate_circle_coords and developed in generate_rec_coords for comppads
    [default.gbr, test2_offseted.gbr]
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2023-06-08 bug fixes
    [PSU controller-B_Cu.gbr, mirrored_and_offseted.gbr, test2.gbr]
2023-06-08 Bug Fixes after gerber.mirror() implementation
    [gcode_tools.py]
2023-06-08 CLI bug fix and --laser-debug implemented
    [gcode_tools.py]
2023-06-16 Fixing the unipolar driver bug
    [main.c, software_uart.c, tmr1_module.c]
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2023-06-21 Finally found a way to implement FULL software uart on pic12f675
    [Config_1.txt, Config_2.txt]
2023-07-11 all files updated after OS change for some reason
    [Config_1.txt, Config_2.txt, DC_Motor_Driver.kicad_pcb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]
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2023-07-26 Started new project PCB clamping system
    [configuration_bits.h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]
2023-07-31 Fixed numerous bugs in CAM module and marked numerous others
    [unipolar stepper driver.kicad_pcb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]
2023-08-02 Further bug fixing for unipolar_driver.gbr CAM module
    [gcode_tools.py]
2023-08-04 one bug remaining for unipolar_driver.gbr cam module test case
    [gcode_tools.py]
2023-08-04 Bug fix finished for unipolar_driver.gbr :)
    [gcode_tools.py]
2023-10-18 unipolar circuit development
    [unipolar stepper driver.kicad_pcb, unipolar stepper driver.kicad_sch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]
2023-10-30 Finished PWM Multiplexer circuit schematics and started PCB design
    [PWM Multiplexer.kicad_pcb, PWM Multiplexer.kicad_sch]
2023-10-31 Fixed diode directions in unipolar_driver circuit
    [unipolar stepper driver.csv, unipolar stepper driver.kicad_pcb, unipolar stepper driver.kicad_sch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]
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2023-10-31 PWM multiplexer circuit PCB traces ALL connected in a preliminary manner
    [PWM Multiplexer.kicad_pcb, PWM Multiplexer.kicad_sch]
2023-11-01 Further development in PWM Multiplexer circuit PCB final design
    [PWM Multiplexer.kicad_pcb]
2023-11-11 looks like CAM module needs bug fixing again
    [unipolar stepper driver.kicad_sch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]
2023-11-18 minor changes
    [PSU controller.csv, limit_switch.kicad_pcb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]
2023-11-19 Finished limit switch circuit and minor changes to cam module
    [limit_switch.kicad_pcb, limit_switch.kicad_sch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]
2023-11-19 Fixed DC Motor Circuit and discovered fatal design flaw in PWM demultiplexer
    [DC_Motor_Driver.kicad_pcb, DC_Motor_Driver.kicad_sch, PWM Multiplexer.kicad_pcb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]
2023-11-26 redesigning PWM Multiplexer PCB Solution
    [PWM Multiplexer.kicad_pcb]
2023-11-27 Further development in PWM Multiplexer PCB solution
    [PWM Multiplexer.kicad_pcb]
2023-11-29 added passive filters to limit switch circuit
    [limit_switch.csv, limit_switch.kicad_pcb, limit_switch.kicad_sch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]
2023-12-13 Implemented Isolators in PWM Mutliplexer
    [DC_Motor_Driver.kicad_pcb, DC_Motor_Driver.kicad_sch, PWM Multiplexer.kicad_pcb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]
2023-12-13 added optical isolation to PWM demultiplexer circuit schematic
    [PWM Multiplexer.kicad_pcb, PWM Multiplexer.kicad_sch]
2024-01-10 finished PWM multiplexer circuit final version
    [PWM Multiplexer.kicad_pcb, PWM Multiplexer.kicad_sch, PWM_Multiplexer.kicad_pcb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]
2024-01-10 DC Motor Driver Circuit fine tuning for manufacturing
    [DC_Motor_Driver.csv, DC_Motor_Driver.kicad_pcb, DC_Motor_Driver.kicad_sch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]
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2024-02-16 further development in esp32-cam
    [PSU controller.kicad_pcb, PWM_Multiplexer.kicad_sch, limit_switch.kicad_pcb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]
2024-02-26 Added some gerber files and gcode files for some of the circuit pcbs
    [PSU controller-B_Cu.gbr, mirrored_and_offseted.gbr]
2024-06-03 removed .ca folder
    [Config_1.txt, Config_2.txt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]
2024-09-24 added .step file and some media
    [PWM_Multiplexer.kicad_pcb]
2024-09-24 cleaned Programming file
    [alarm_codes_en_US.csv, build_option_codes_en_US.csv, config.h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]
